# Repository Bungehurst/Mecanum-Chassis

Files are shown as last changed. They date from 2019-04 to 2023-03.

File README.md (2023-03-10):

# Introduction 
- This experimental project is about building a mecanum mobile chassis from zero to one. The whole project contains mechanical design, PCB design, FPGA, and STM32 programming.
- The FPGA programmes are here: https://github.com/Bungehurst/FPGA-Mecanum-Chassis
- CSDN here: https://lun55423.blog.csdn.net/article/details/107223313
<div align="center">
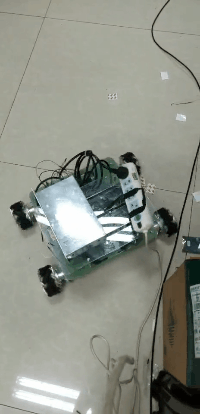
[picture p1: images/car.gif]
video
    
</div>

# Mechanical Model
<p align="center">
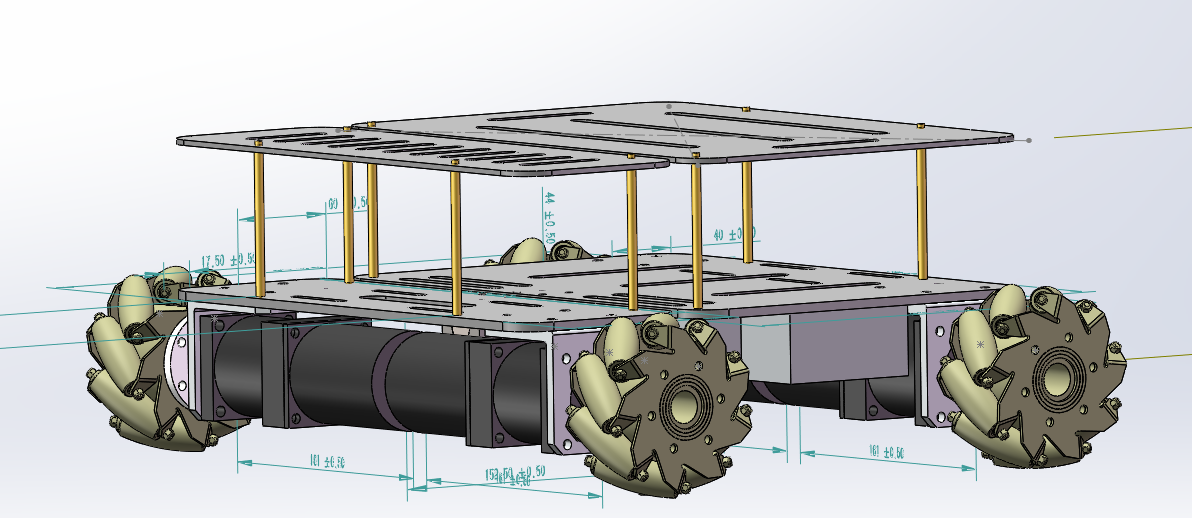
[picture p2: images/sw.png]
    <br>
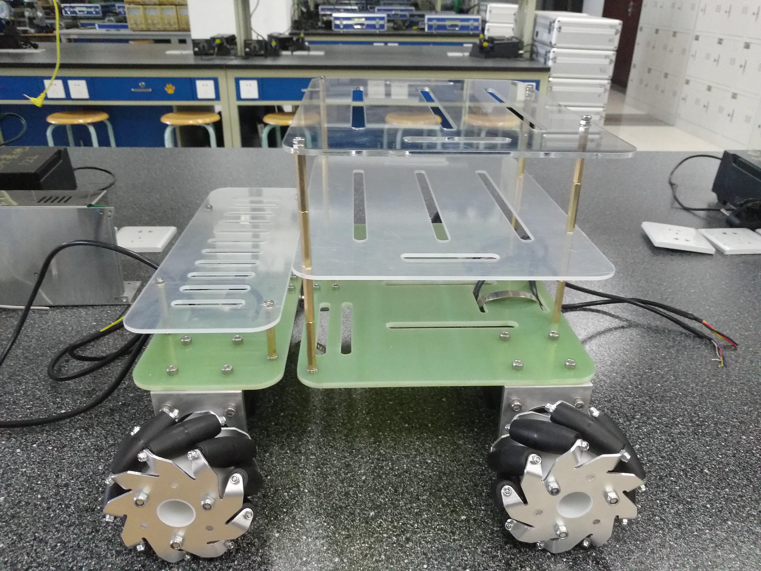
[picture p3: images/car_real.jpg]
    
</p>

# PCB Design
<p align="center">
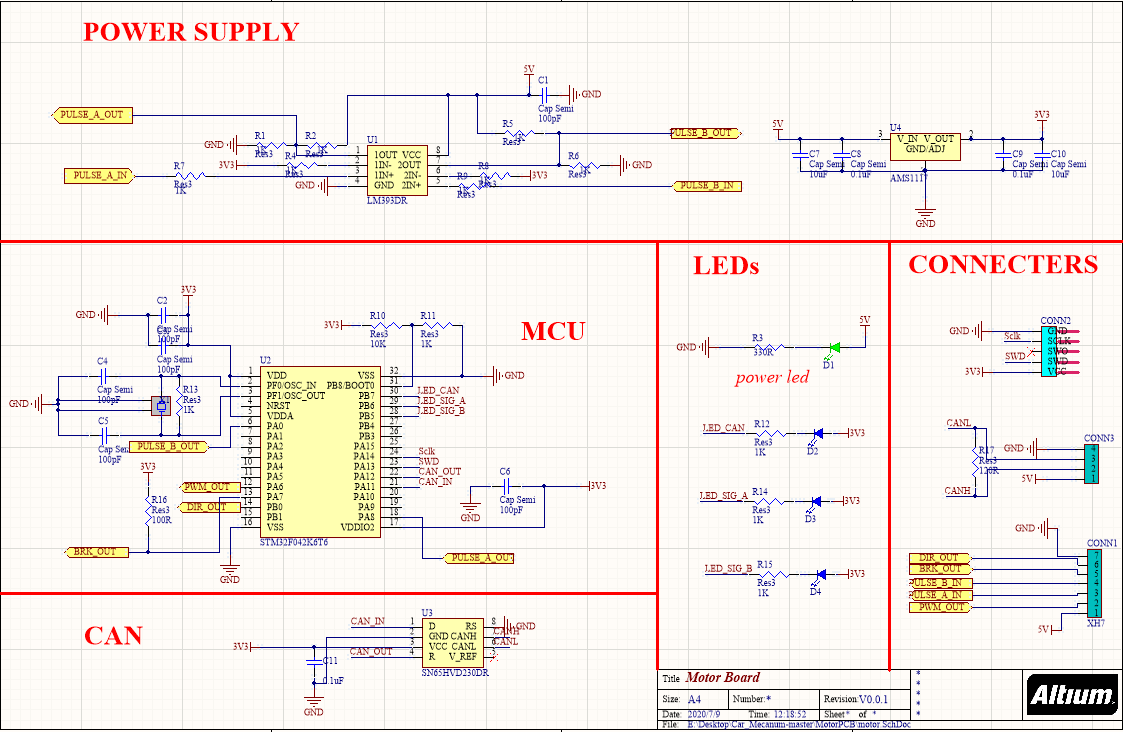
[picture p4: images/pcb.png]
    <br>
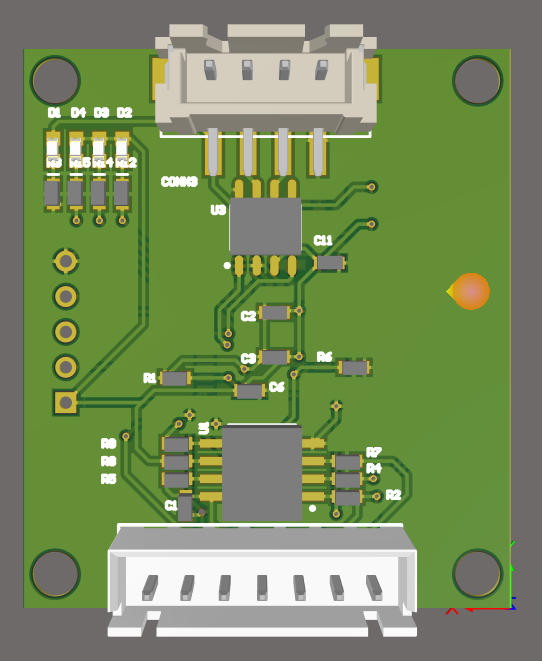
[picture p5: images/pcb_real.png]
    
</p>

# FPGA Design
<p align="center">
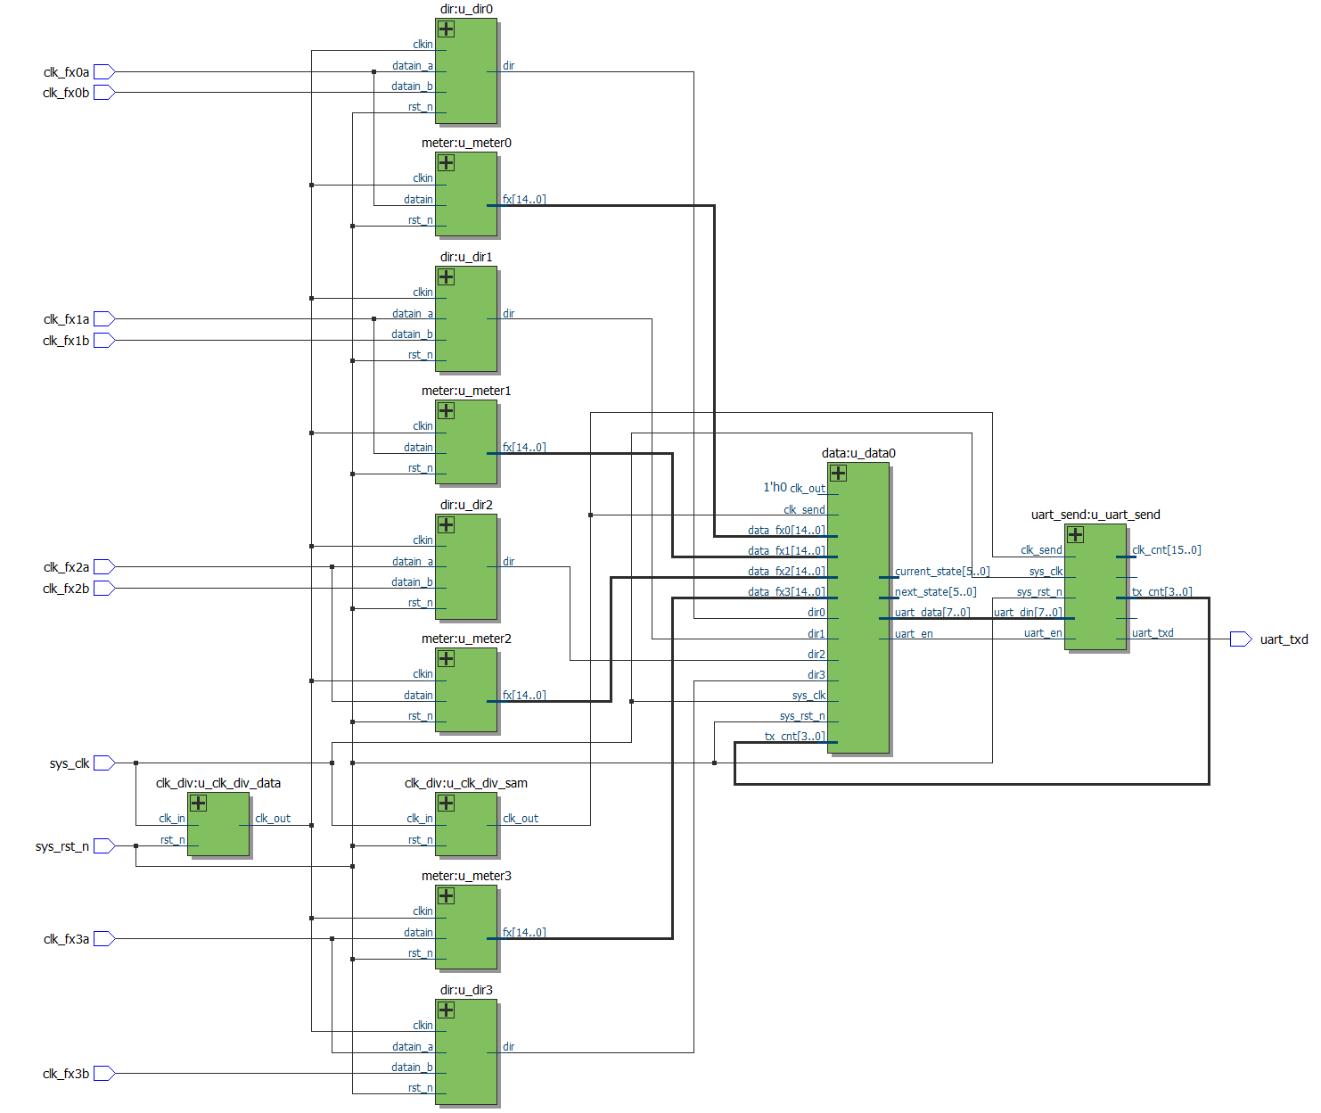
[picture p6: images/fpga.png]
    
</p>

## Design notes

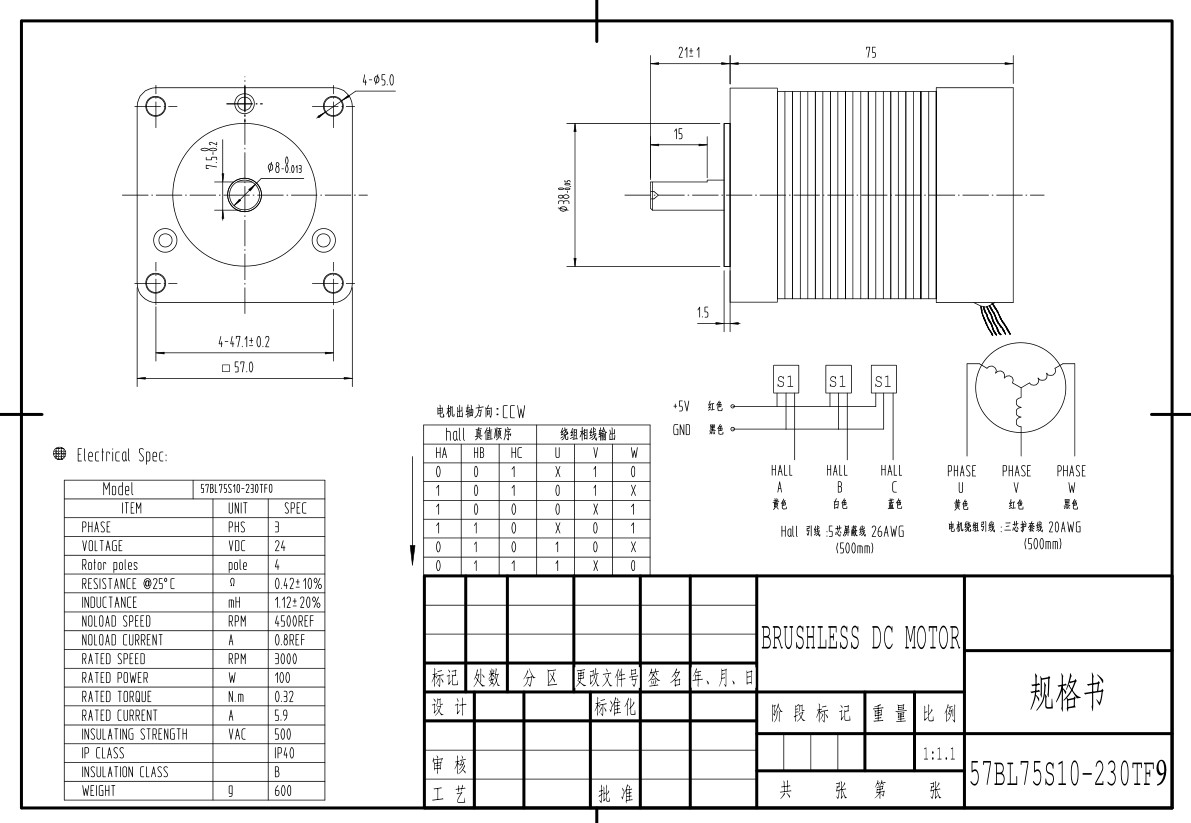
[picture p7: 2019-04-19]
Datasheet/电机/电机.jpg

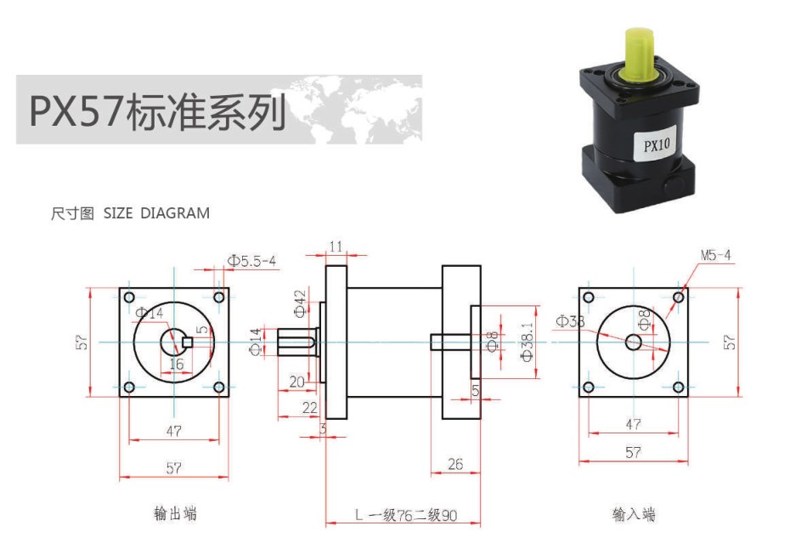
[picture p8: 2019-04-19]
Datasheet/减速箱/减速箱.jpg

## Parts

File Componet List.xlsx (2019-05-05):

序号 | 名称 | 单价 | 数量 | 价格 | 备注
1 | 57直流无刷电机 | 118 | 4 | 472 | 57BL75S10-230TF9 0.32NM 3000rpm 100w 5.9A
2 | 57减速箱 | 175 | 4 | 700 | 减速比 10：1
3 | 电机支架（定制） | 60 | 4 | 240
4 | 直流无刷电机驱动板 | 49 | 5 | 245 | 3.3v pwm控制 三相有霍尔 | （烧了一个）加购一个
5 | 麦克纳姆轮 | 510 | 1 | 510 | 一组4个 直径 100mm
6 | 共轴双板连接器 | 56 | 1 | 56 | 大号
7 | 法兰联轴器 | 200 | 1 | 200 | 14mm 有键槽
8 | 底盘玻纤板（定制） | 140 | 1 | 140 | 前后两块
9 | 甲板亚克力（定制） | 30 | 1 | 30 | 前后两块
10 | 螺丝螺母 | 54.6 | 1 | 54.6
11 | 管扎 | 1.14 | 8 | 9.12
12 | 3M胶 | 15 | 1 | 15 | 40 pieces
13 | 电池 | 458 | 1 |  | 24v 10ah 放电电流30a（移动用）
14 | DC-DC降压模块 | 19.5 | 1 |  | 24vTo5v 8.5a 80W
15 | 明纬开关电源 | 160 | 1 | 160 | 24v 30a 720W (调试用)
16 | TF卡 | 126 | 1 | 126 | 三星 64g UHS-1
17 | Nvidia Jetson Nano | 899 | 1 | 899
18 | 运费 | 126 | 1 | 126
 |  |  |  |  | 合计 | 3982.72

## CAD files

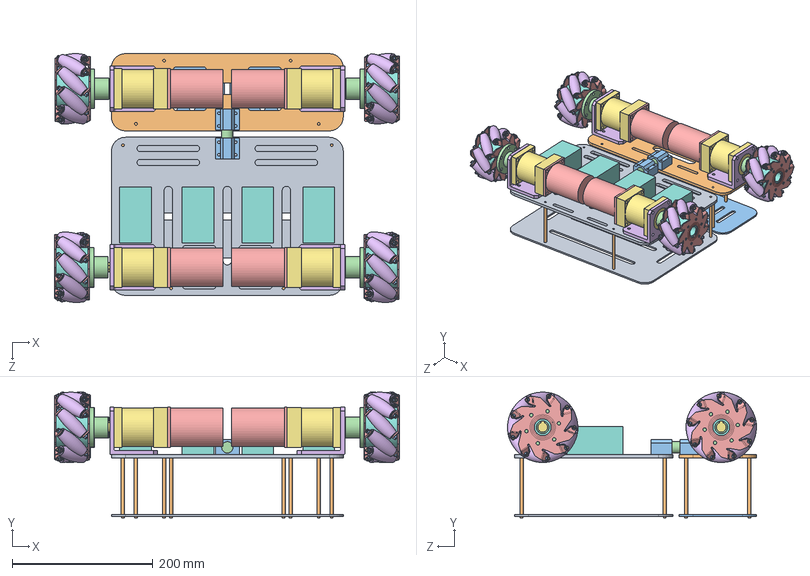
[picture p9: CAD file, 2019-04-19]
Solidworks/底盘装配体.SLDASM
490.8 x 179.2 x 354.1 mm
底盘后轮
底盘前轮
共轴器1 x 2
共轴器2
电机 x 4
电机支架 x 4
减速箱 x 4
电机驱动器 x 4
甲板
铜柱 x 8
甲板前
法兰联轴器 x 4
BM6 x 8
PRT0002 x 36
BM1 x 36
BM4 x 4
BM7 x 72
BM8 x 72
BM9 x 72

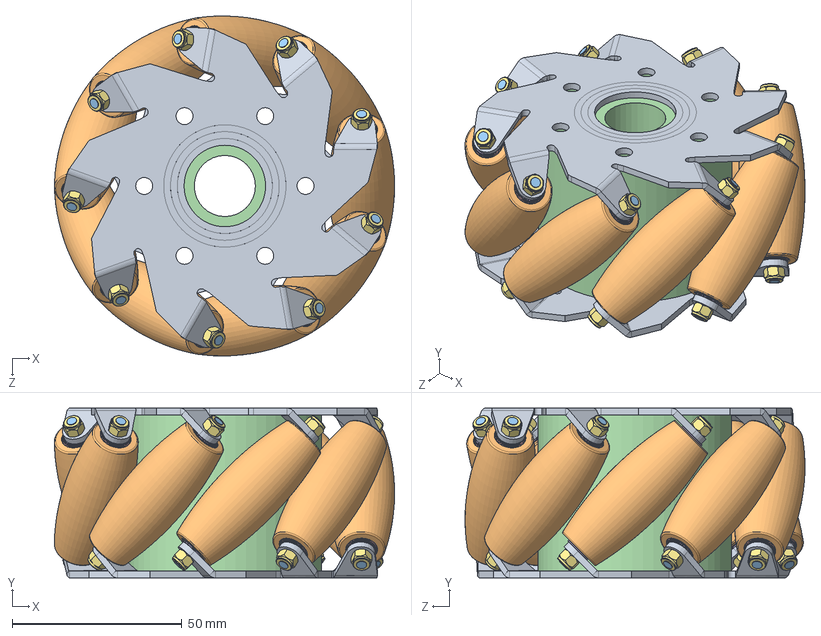
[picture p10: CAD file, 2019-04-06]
Solidworks/100mm麦轮模型/100mm Aluminum Mecanum wheels.SLDASM
100.2 x 50.0 x 100.1 mm
BM6 x 2
PRT0002 x 9
BM1 x 9
BM4
BM7 x 18
BM8 x 18
BM9 x 18

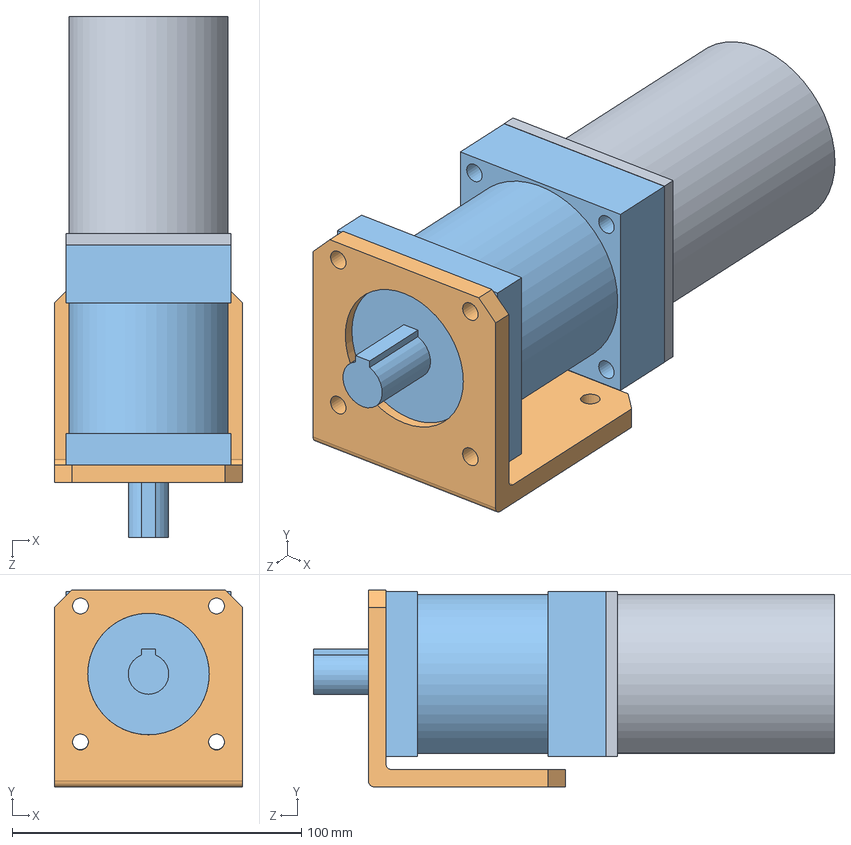
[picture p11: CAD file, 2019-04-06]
Solidworks/电机装配体SLDASM.SLDASM
65.0 x 68.0 x 180.0 mm
电机
电机支架
减速箱

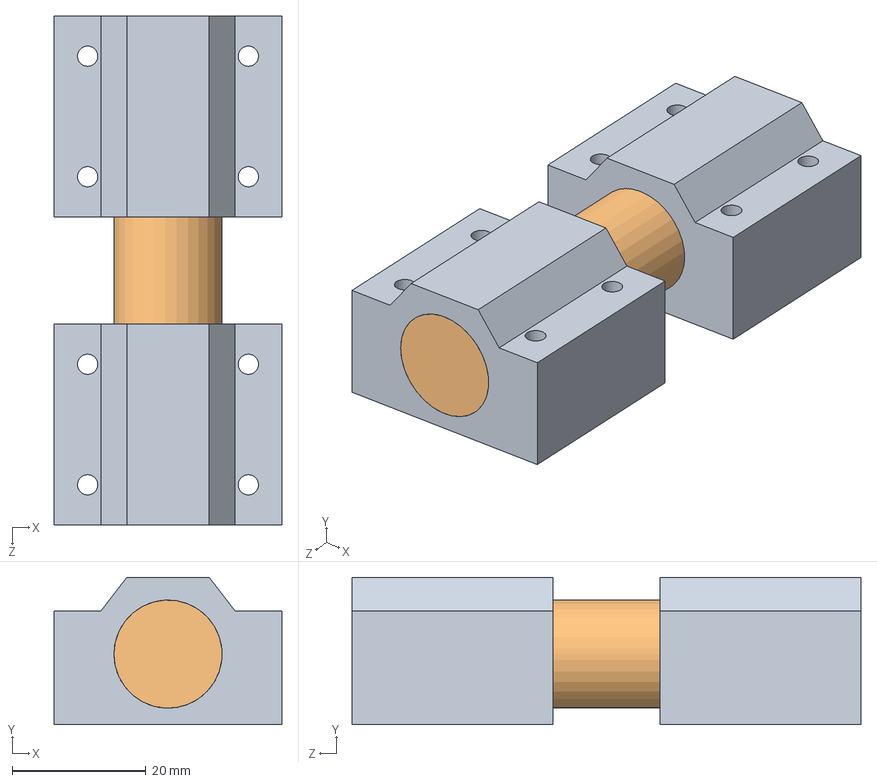
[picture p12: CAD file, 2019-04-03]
Solidworks/共轴器装配体.SLDASM
34.0 x 22.0 x 76.0 mm
共轴器1 x 2
共轴器2

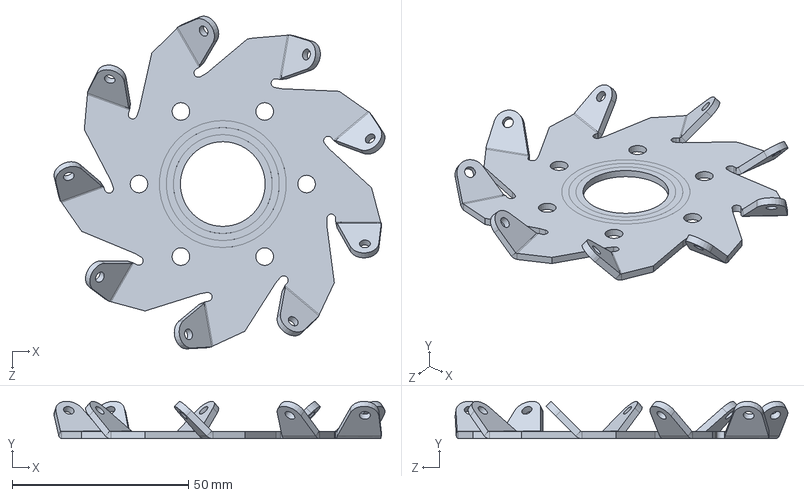
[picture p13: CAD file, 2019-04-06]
Solidworks/100mm麦轮模型/BM6.sldprt
93.8 x 10.6 x 94.3 mm

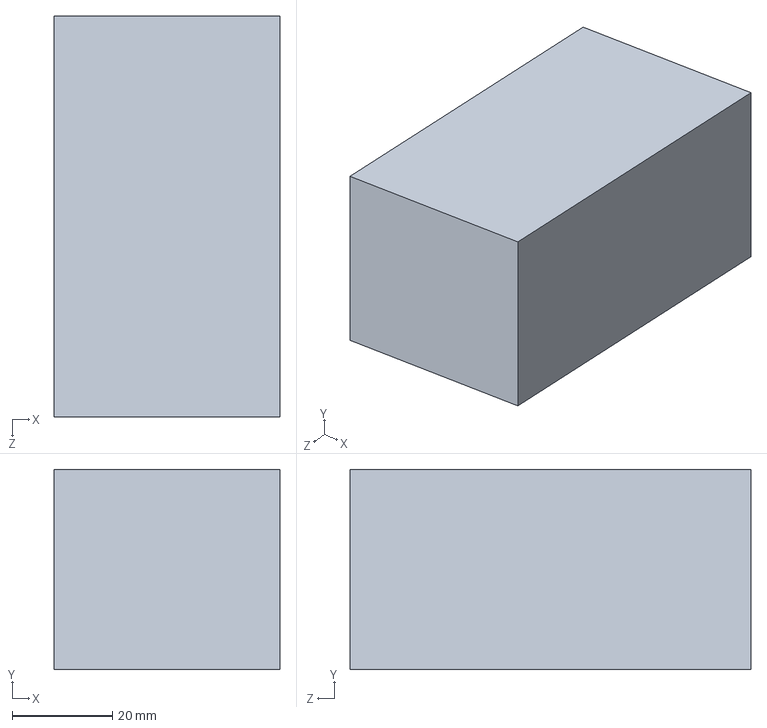
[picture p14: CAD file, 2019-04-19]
Solidworks/电机驱动器.SLDPRT
45.0 x 40.0 x 80.0 mm

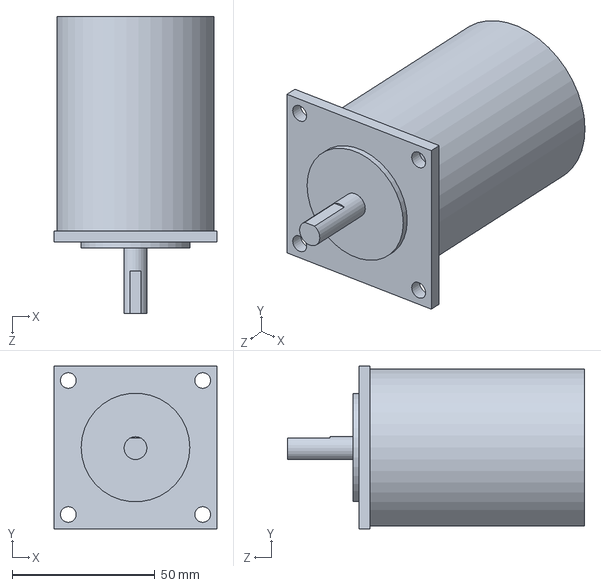
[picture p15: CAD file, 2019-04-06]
Solidworks/电机.SLDPRT
57.0 x 57.0 x 104.0 mm

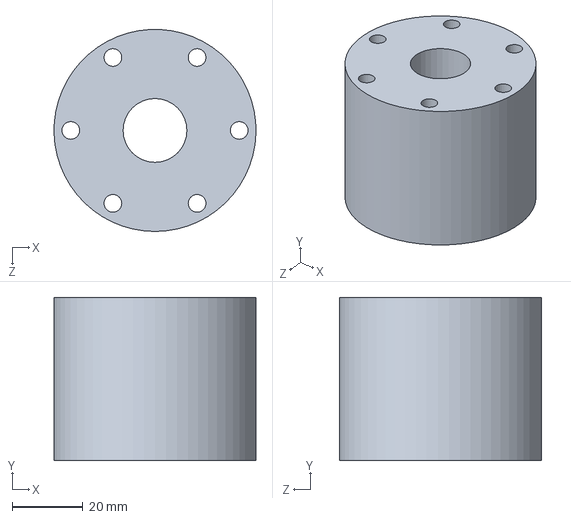
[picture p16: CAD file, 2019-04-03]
Solidworks/100mm麦轮模型/BM4.sldprt
57.0 x 46.0 x 57.0 mm

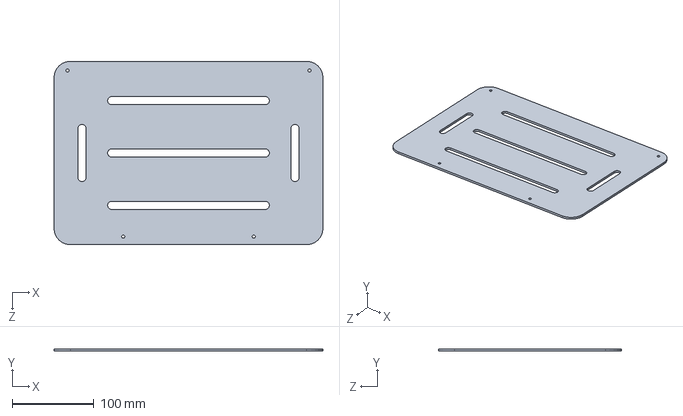
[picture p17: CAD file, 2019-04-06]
Solidworks/甲板.SLDPRT
330.0 x 3.00 x 225.0 mm

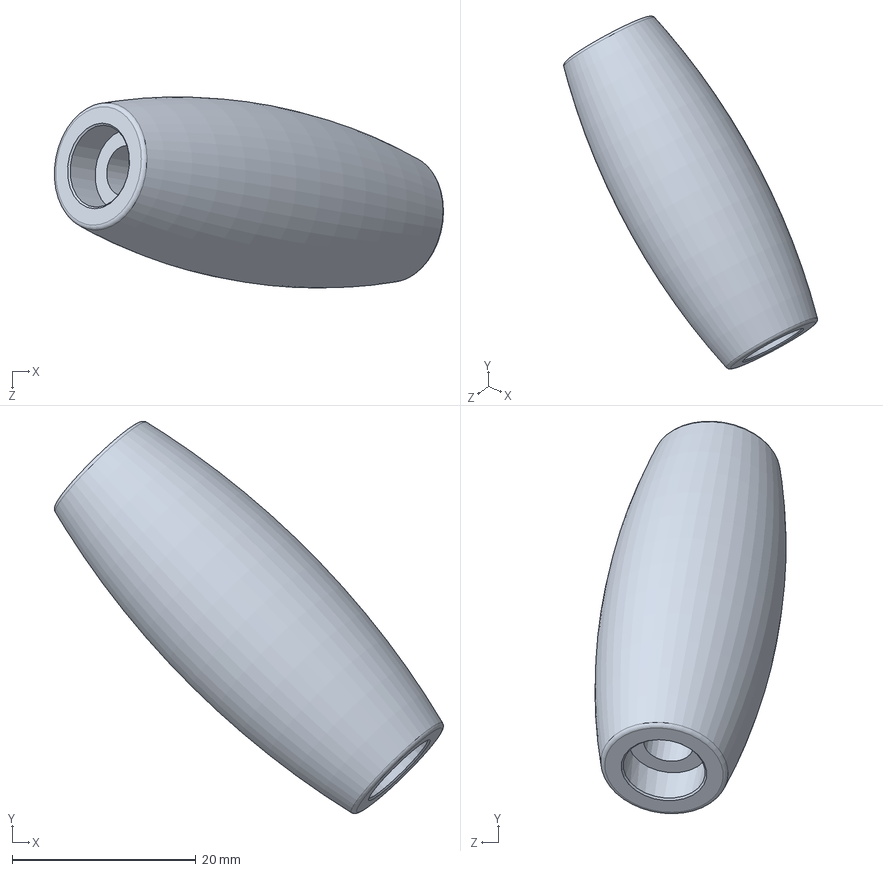
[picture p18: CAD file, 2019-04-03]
Solidworks/100mm麦轮模型/PRT0002.sldprt
42.3 x 42.7 x 20.8 mm

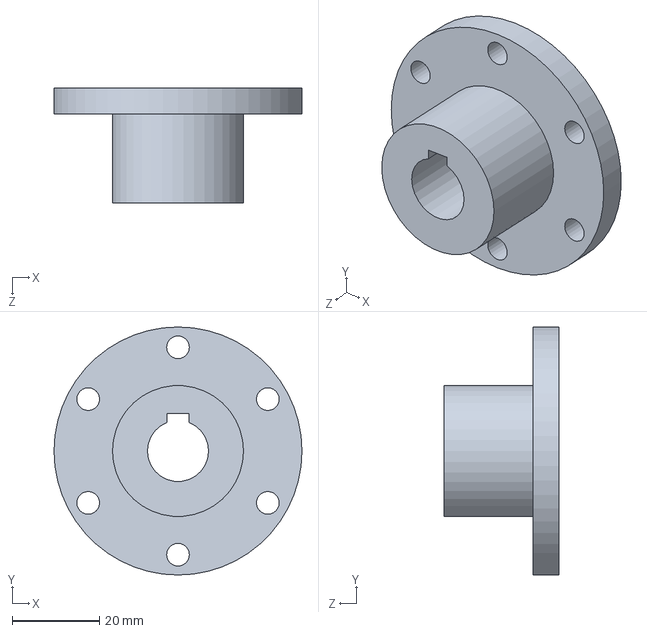
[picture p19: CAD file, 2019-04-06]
Solidworks/法兰联轴器.SLDPRT
56.8 x 56.8 x 26.4 mm

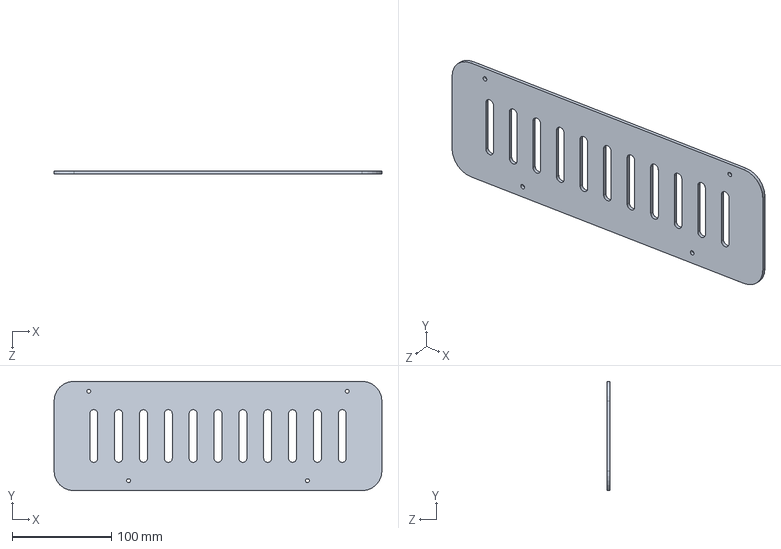
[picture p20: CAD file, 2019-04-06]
Solidworks/甲板前.SLDPRT
330.0 x 110.0 x 3.00 mm

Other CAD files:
Solidworks/CAD/电机支架 (右视).DWG
Solidworks/CAD/电机支架 (前视).DWG
Solidworks/100mm麦轮模型/BM1.sldprt
Solidworks/CAD/电机支架 (上视).DWG
Solidworks/100mm麦轮模型/BM7.sldprt
Solidworks/100mm麦轮模型/BM9.sldprt
Solidworks/100mm麦轮模型/BM8.sldprt
Solidworks/CAD/底盘前轮.DWG
Solidworks/CAD/底盘前轮.SLDDRW
Solidworks/CAD/底盘后轮.DWG
Solidworks/CAD/底盘后轮.SLDDRW
Solidworks/CAD/甲板.DWG
Solidworks/CAD/甲板.SLDDRW
Solidworks/CAD/甲板前.DWG
Solidworks/CAD/甲板前.SLDDRW
Solidworks/CAD/电机支架.DWG
Solidworks/CAD/电机支架.SLDDRW
Solidworks/共轴器1.SLDPRT
Solidworks/共轴器2.SLDPRT
Solidworks/减速箱.SLDPRT
Solidworks/底盘前轮.SLDPRT
Solidworks/底盘后轮.SLDPRT
Solidworks/底盘装配体.SLDDRW
Solidworks/电机支架.SLDPRT
Solidworks/轮子.SLDPRT
Solidworks/铜柱.SLDPRT

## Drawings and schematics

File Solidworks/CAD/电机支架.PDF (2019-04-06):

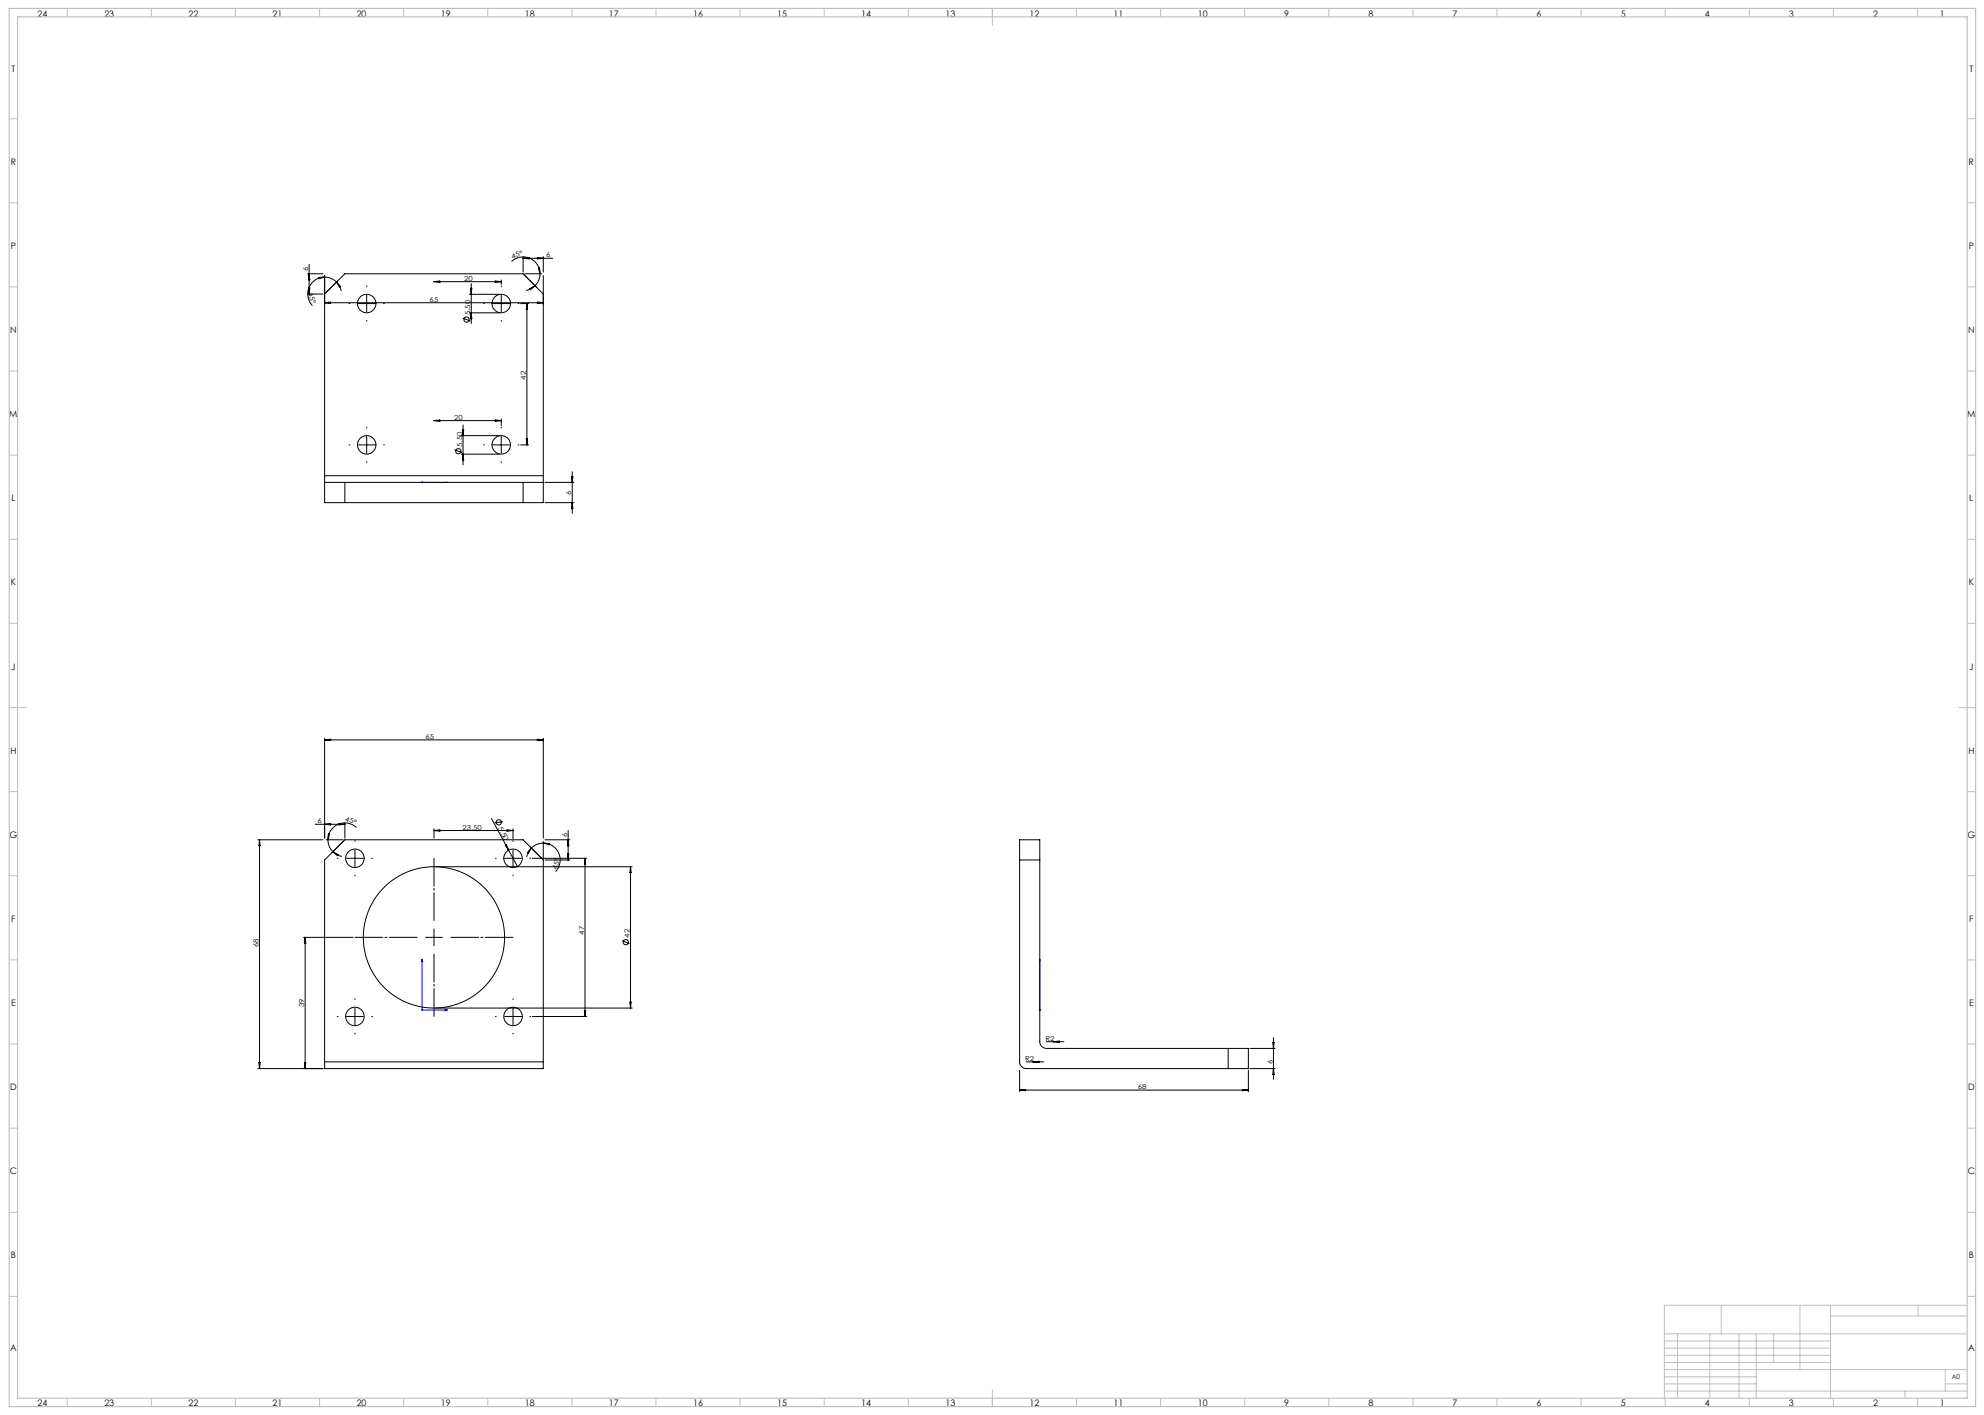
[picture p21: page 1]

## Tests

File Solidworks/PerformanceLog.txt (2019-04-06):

Mesh Preparation:  0 hr 0 min 1 sec
Creating midsurfaces by SW:  0 hr 0 min 0 sec
Standard solid mesh assembly imprint:  0 hr 0 min 0 sec
Standard solid mesh bolt head imprint and hard point processing:  0 hr 0 min 0 sec
Standard solid mesh total preparation including imprint:  0 hr 0 min 0 sec
Standard surface meshing for Solid Mesh:  0 hr 0 min 0 sec
Standard volume meshing for Solid Mesh:  0 hr 0 min 0 sec
Standard solid mesh arranging data:  0 hr 0 min 0 sec
Standard solid mesh total:  0 hr 0 min 0 sec
Standard shell (non-midsurf) mesh joint, bolt head, hard point imprint:  0 hr 0 min 1 sec
Standard shell (non-midsurf) mesh total preparation:  0 hr 0 min 1 sec
Standard shell (non-midsurf) mesh surface mesh:  0 hr 0 min 0 sec
Standard shell (non-midsurf) mesh arranging data:  0 hr 0 min 0 sec
Re-align shell mesh and normal, jacobian check:  0 hr 0 min 0 sec
Standard (non-midsurf) shell mesh total:  0 hr 0 min 1 sec
Standard midsurf mesh total:  0 hr 0 min 0 sec
Beam mesh:  0 hr 0 min 0 sec
Preparing to transfer data:  0 hr 0 min 3 sec
Processing material properties:  0 hr 0 min 0 sec
Processing element groups:  0 hr 0 min 0 sec
Processing drop test gap nodes:  0 hr 0 min 0 sec
Updating thickness for shell regions:  0 hr 0 min 0 sec
Processing rconst for elements:  0 hr 0 min 0 sec
Processing egroups:  0 hr 0 min 0 sec
Transferring loads and boundary conditions:  0 hr 0 min 1 sec
Generating body pairs to check contact:  0 hr 0 min 0 sec
Generating contacts:  0 hr 0 min 0 sec
Number of Contacts: 3
Transfer SL1 data:  0 hr 0 min 0 sec
Generate more accurate contact data:  0 hr 0 min 0 sec
Number of contact data: 891
Transfer beam/joint contact data:  0 hr 0 min 0 sec
Transferring other special loads:  0 hr 0 min 0 sec
Transferring bearing loads:  0 hr 0 min 0 sec
Transferring mass elements:  0 hr 0 min 0 sec
Transferring point loads:  0 hr 0 min 0 sec
Transferring distributed beam loads:  0 hr 0 min 0 sec
Transferring rigid bodies:  0 hr 0 min 0 sec
Transferring component no penetration:  0 hr 0 min 0 sec
Writing Data:  0 hr 0 min 0 sec
Transferring analysis options:  0 hr 0 min 0 sec
Total midsurf mapping:  0 hr 0 min 0 sec

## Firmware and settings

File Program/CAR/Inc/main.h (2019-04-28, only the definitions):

#define PC_TX_Pin GPIO_PIN_2
#define PC_TX_GPIO_Port GPIOA
#define PC_RX_Pin GPIO_PIN_3
#define PC_RX_GPIO_Port GPIOA
#define WHEEL_3_PWM_Pin GPIO_PIN_0
#define WHEEL_3_PWM_GPIO_Port GPIOB
#define WHEEL_4_PWM_Pin GPIO_PIN_1
#define WHEEL_4_PWM_GPIO_Port GPIOB
#define WIRELESS_TX_Pin GPIO_PIN_10
#define WIRELESS_TX_GPIO_Port GPIOB
#define WIRELESS_RX_Pin GPIO_PIN_11
#define WIRELESS_RX_GPIO_Port GPIOB
#define WHEEL_4P_Pin GPIO_PIN_12
#define WHEEL_4P_GPIO_Port GPIOB
#define WHEEL_3P_Pin GPIO_PIN_13
#define WHEEL_3P_GPIO_Port GPIOB
#define WHEEL_2P_Pin GPIO_PIN_14
#define WHEEL_2P_GPIO_Port GPIOB
#define WHEEL_1P_Pin GPIO_PIN_15
#define WHEEL_1P_GPIO_Port GPIOB
#define WHEEL_4_Pin GPIO_PIN_8
#define WHEEL_4_GPIO_Port GPIOA
#define WHEEL_3_Pin GPIO_PIN_9
#define WHEEL_3_GPIO_Port GPIOA
#define WHEEL_2_Pin GPIO_PIN_10
#define WHEEL_2_GPIO_Port GPIOA
#define WHEEL_1_Pin GPIO_PIN_11
#define WHEEL_1_GPIO_Port GPIOA
#define LED_COM_Pin GPIO_PIN_15
#define LED_COM_GPIO_Port GPIOA
#define LED_SYS_Pin GPIO_PIN_3
#define LED_SYS_GPIO_Port GPIOB
#define WHEEL_1_PWM_Pin GPIO_PIN_4
#define WHEEL_1_PWM_GPIO_Port GPIOB
#define WHEEL_2_PWM_Pin GPIO_PIN_5
#define WHEEL_2_PWM_GPIO_Port GPIOB
#define LED_WHEEL_4_Pin GPIO_PIN_6
#define LED_WHEEL_4_GPIO_Port GPIOB
#define LED_WHEEL_3_Pin GPIO_PIN_7
#define LED_WHEEL_3_GPIO_Port GPIOB
#define LED_WHEEL_2_Pin GPIO_PIN_8
#define LED_WHEEL_2_GPIO_Port GPIOB
#define LED_WHEEL_1_Pin GPIO_PIN_9
#define LED_WHEEL_1_GPIO_Port GPIOB

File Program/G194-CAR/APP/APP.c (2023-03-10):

#include "APP.h"
#include <math.h>
#include "usart2.h"
#include "usart3.h"

#define Kp_LF 0.49f
#define Ki_LF 0.001f
#define Kd_LF 0.0f

#define Kp_RF 0.49f
#define Ki_RF 0.001f
#define Kd_RF 0.0f

#define Kp_LB	0.489f
#define Ki_LB 0.001f
#define Kd_LB 0.0f

#define Kp_RB 0.481f
#define Ki_RB 0.001f
#define Kd_RB 0.0f

PID_GENERAL PID_LF = {Kp_LF,\
											Ki_LF,\
											Kd_LF,\
											{0,0},\
											0,\
											0,\
											0				};
PID_GENERAL PID_RF = {Kp_RF,\
											Ki_RF,\
											Kd_RF,\
											{0,0},\
											0,\
											0,\
											0				};
PID_GENERAL PID_LB = {Kp_LB,\
											Ki_LB,\
											Kd_LB,\
											{0,0},\
											0,\
											0,\
											0				};
PID_GENERAL PID_RB = {Kp_RB,\
											Ki_RB,\
											Kd_RB,\
											{0,0},\
											0,\
											0,\
											0				};

#define Kp_LINE_RHO 30.0f
#define Ki_LINE_RHO 0.0f
#define Kd_LINE_RHO 0.0f

#define Kp_LINE_THETA 30.0f
#define Ki_LINE_THETA 0.0f
#define Kd_LINE_THETA 0.0f

											
#define 		RHO_MAX				90.0f
#define			THETA_MAX			80.0f
											
PID_LINE	PID_LINE_RHO = {	Kp_LINE_RHO,\
														Ki_LINE_RHO,\
														Kd_LINE_RHO,\
														{0,0},\
														0,\
														0,\
														0,\
														-RHO_MAX,\
														RHO_MAX,\
														-1500,\
														1500};
	
PID_LINE	PID_LINE_THETA = {	Kp_LINE_THETA,\
															Ki_LINE_THETA,\
															Kd_LINE_THETA,\
															{0,0},\
															0,\
															0,\
															0,\
															-THETA_MAX,\
															THETA_MAX,\
															-1500,\
															1500};
	
enum Wheel_Num{W_LF = 0,W_RF = 1,W_LB = 2,W_RB = 3};
void Set_Wheel_Speed(int16_t target,CAR_WHEEL *wheel,PID_GENERAL *pid,uint8_t Wheel_Num)
{
	Wheel_PID(wheel->speed,target,pid);
	switch(Wheel_Num)
	{
		case W_LF:
			if(pid->output > 0)	
			{
				DIR_CTL_LF(Bit_SET);
				PWM_F_L(fabs(pid->output));
			}
			else {
				DIR_CTL_LF(Bit_RESET);
				PWM_F_L(fabs(pid->output));
			}
			break;
		case W_RF:
			if(pid->output > 0)	
			{
				DIR_CTL_RF(Bit_SET);
				PWM_F_R(fabs(pid->output));
			}
			else {
				DIR_CTL_RF(Bit_RESET);
				PWM_F_R(fabs(pid->output));
			}
			break;
		case W_LB:
			if(pid->output > 0)	
			{
				DIR_CTL_LB(Bit_SET);
				PWM_B_L(fabs(pid->output));
			}
			else {
				DIR_CTL_LB(Bit_RESET);
				PWM_B_L(fabs(pid->output));
			}
			break;
		case W_RB:
			if(pid->output > 0)	
			{
				DIR_CTL_RB(Bit_SET);
				PWM_B_R(fabs(pid->output));
			}
			else {
				DIR_CTL_RB(Bit_RESET);
				PWM_B_R(fabs(pid->output));
			}
			break;
		default: break;
	}
}

void Motor_Control(void)
{
	static int16_t channel_1 = 0,channel_2 = 0,channel_4 = 0;//channel_3 = 0
	
	channel_1 = -rc_data.Channel_Current[2]/800.0f*10000*0.5f;	//throttle
	channel_2 = rc_data.Channel_Current[0]/800.0f*10000*0.5f;		//rotate
	//channel_3 = rc_data.Channel_Current[1]/800.0f*10000*0.5f;		// no use
	channel_4 = -rc_data.Channel_Current[3]/800.0f*10000*0.5f;	//shift-left/right

	Set_Wheel_Speed(channel_1-channel_4-channel_2,&Car_Wheel_LF,&PID_LF,W_LF);//-
	Set_Wheel_Speed(-channel_1-channel_4-channel_2,&Car_Wheel_RF,&PID_RF,W_RF);
	Set_Wheel_Speed(channel_1+channel_4-channel_2,&Car_Wheel_LB,&PID_LB,W_LB);//-
	Set_Wheel_Speed(-channel_1+channel_4-channel_2,&Car_Wheel_RB,&PID_RB,W_RB);

}
float output_rho = 0,output_theta = 0,channel_1 = 0;
void APP_Init(void)
{
	if(Openmv.theta > 90.0f && Openmv.theta < 175.0f)
	{
		Openmv.delta_theta = Openmv.theta - 180.0f ;
		if(Openmv.rho > 0)
		{
			Openmv.delta_rho = Openmv.rho - fabsf(40.0f*sinf(Openmv.theta) + 30.0f*cosf(Openmv.theta));
			Openmv.delta_x = -Openmv.delta_rho / cosf(180.0f - Openmv.theta);	
		}else
		{
			Openmv.delta_rho = Openmv.rho + fabsf(40.0f*sinf(Openmv.theta) + 30.0f*cosf(Openmv.theta));
			Openmv.delta_x = -Openmv.delta_rho / cosf(180.0f - Openmv.theta);	
		}
	}
	else if(Openmv.theta < 90.0f && Openmv.theta > 5.0f )
	{
		Openmv.delta_theta = Openmv.theta ;
		Openmv.delta_rho = Openmv.rho - fabsf(40.0f*sinf(Openmv.theta) + 30.0f*cosf(Openmv.theta));
		Openmv.delta_x = Openmv.delta_rho / cosf(Openmv.theta);
	}else
	{
		Openmv.delta_theta = 0;
		if(Openmv.theta > 175.0f)
		{
			if(Openmv.rho > 0)
			{
				Openmv.delta_rho = Openmv.rho - fabsf(40.0f*sinf(Openmv.theta) + 30.0f*cosf(Openmv.theta));
				Openmv.delta_x = -Openmv.delta_rho / cosf(180.0f - Openmv.theta);	
			}else
			{
				Openmv.delta_rho = Openmv.rho + fabsf(40.0f*sinf(Openmv.theta) + 30.0f*cosf(Openmv.theta));
				Openmv.delta_x = -Openmv.delta_rho / cosf(180.0f - Openmv.theta);	
			}
		}
		else if(Openmv.theta < 5.0f)
		{
			Openmv.delta_rho = Openmv.rho - fabsf(40.0f*sinf(Openmv.theta) + 30.0f*cosf(Openmv.theta));
			Openmv.delta_x = Openmv.delta_rho / cosf(Openmv.theta);
		}
	}
	channel_1 = 800.0f;
	output_rho = PID_General(0,Openmv.delta_x,&PID_LINE_RHO);
	output_theta = PID_General(0,Openmv.delta_theta,&PID_LINE_THETA);

	Set_Wheel_Speed(channel_1-output_rho-output_theta,&Car_Wheel_LF,&PID_LF,W_LF);//-
	Set_Wheel_Speed(-channel_1-output_rho-output_theta,&Car_Wheel_RF,&PID_RF,W_RF);
	Set_Wheel_Speed(channel_1+output_rho-output_theta,&Car_Wheel_LB,&PID_LB,W_LB);//-
	Set_Wheel_Speed(-channel_1+output_rho-output_theta,&Car_Wheel_RB,&PID_RB,W_RB);
}

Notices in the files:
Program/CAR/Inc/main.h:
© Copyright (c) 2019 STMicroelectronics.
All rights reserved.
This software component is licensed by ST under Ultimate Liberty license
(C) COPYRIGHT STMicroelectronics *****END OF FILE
